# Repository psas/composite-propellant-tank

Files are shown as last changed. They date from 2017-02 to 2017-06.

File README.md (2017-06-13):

# composite-propellant-tank
Prototyping lightweight composite LOX and IPA tanks for LV4.

**The good**: the current PSAS CF airframe technology seems to offer fantastic tank factors if they can be used as propellant tanks, even given extremely conservative mass growth assumptions. This could give us the mass ratios to get LV4 above the von Karman line. Early conceptual design analysis for LV4 suggests that 280x700 mm modules are optimal.

**The bad**: Composites are hard...
- Lack of established design criteria for composite tanks
- Galvanic corrosion of composites in contact with metals
- Composites degrade under extreme temperatures
- Composites degrade in the presence of mositure
- Difficult to detect defective adhesive bonds in composite structures
- Difficult to maintain hermetic seals
- Difficult to incorperate cutouts
- Significant problems with CTE mismatch when used in conjunction with metallic structures

**The Ugly**:  Proof-of-Concept Composite Fuel Tank designed and built by 2017 PSAS Capstone Team. Currently undergoing testing and refinement.

## Summary of 2017 Tank Capstone Project Design Artifacts
* Analysis
	* Calculations (Hand Calculations and Python Scripts)
	* Finite Element Analysis (Code, Results, and Documentation)

* Design 
	* CAD (Current and Archive)
	* Design Ideas

* Documents
	* AIAA (Paper Abstract)
	* Materials (MDS and Property info
	* ME492 (Capstone Docs)
	* ME493 (Capstone Docs)
	* Research Documents (Literature Review Documents)
	* OSGC (Oregon Space Grant Award Info)
	* Presentations (Resources for project presentation)
	* Resource Documents (How Tos and Readme Docs for Git, Jupyter, etc.)
	* Safety (docs related to chemical safety)
	*  Team Documents  (Team Agenda, Meeting notes, Contacts, etc.)
	*  Templates (Experiment Templates)
	*  Doc Readme and Standards of Documentation
	*  Media (Photos and Videos)
	
*  Manufacturing (Procedural documents)
*  Testing (Test results and procedures)

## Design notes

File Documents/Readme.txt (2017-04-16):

Current Working files should be located here.  Once completed/past date, move to appropriate folder or archive.

~NB

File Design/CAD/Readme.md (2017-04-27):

## Model Naming Conventions
Current working models should be located in the Current Folder.  Once adjustments have been made, please move previous
models/designs into the appropriate Archive.

~NB

CAD Model Naming Convention:

Part numbering convention:
####-A (first two digits are type of part, i.e. rings or end cap...etc, last two digits are iteration #)
Liner: 01 series          Example: 0101 is first liner iteration, 0102 is second liner iteration
Rings: 02 series
End cap: 03 series
Al Tape: 04 series
PRV pipe: 05
Gasket: 06
Letters refer to various versions, such as tube liner vs sheet with seam liner
Example: 0201-A is ring designed for sheet liner iteration 1, 0201-B is ring designed for tube liner iteration 2.

A=Sheet liner, B=Tube liner

## Summary of Iterations so far:

- Tank Iteration 1: (Archive/First Tank Assembly) This is a design with a round end cap. 

- Tank Iteration 2: (Archive/Second_model) Has a flat end cap, screw size is 0-80.

- Tank Iteration 3: (current/Flat End Cap Model (.031-in Sheet Liner)) This model uses the thin PTFE sheet that is etched
on one side for bonding. Screws have been updated to size 3-48. The assembly has two options for end caps. There is a flat
end cap and a bell shaped end cap. The flat endcap requires nuts and washers to attach the threaded fittings. The bell shaped
end cap has threading to attach the fittings. Note: to view the bell shaped endcap suppress End Cap<1> and End Cap <2> and unsuppress 
Alternative End Cap and No Holes End Cap. This design requires an aluminum bridge (not shown) to bond the sheet in a tube shape.

- Tank Iteration 4: (current\Flat End Cap Model (0.125-in Tube Liner)) This model uses an 1/8<sup>th</sup> inch tube of PTFE and has a flat endcap

- Tank Iteration 5: (current\Shrink Fit Model (0.125-in Tube Liner)) End cap was modified for a shrink fit design. The sizing for the fitting
portion will be complete when the size calculations are done. We are also considering adding a keyway for hole alignment.

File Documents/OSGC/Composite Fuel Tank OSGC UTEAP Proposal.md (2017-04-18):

**Composite Cryogenic Fuel Tank**

Portland State University

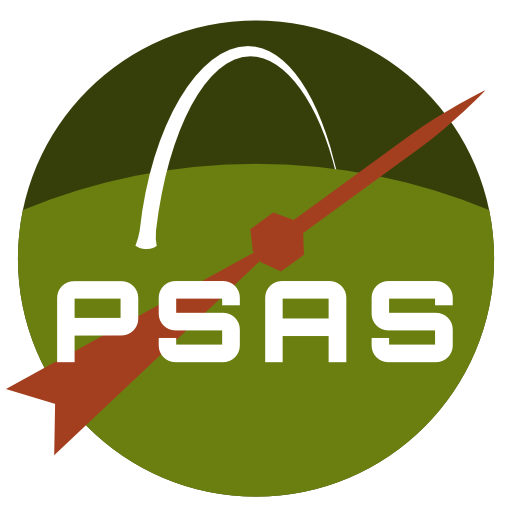
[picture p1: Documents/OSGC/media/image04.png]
{width="1.515625546806649in"
height="1.515625546806649in"}

*Team Lead*

Alex Farias

Undergraduate Student, Department of Mechanical and Materials
Engineering

Portland State University

1323 SE 65th Ave. Hillsboro, OR 97123

(971)770-6017

afarias@pdx.edu

*Project Advisor*

Jun Jiao

Department of Mechanical and Materials Engineering

Portland State University

\(503) 725-4228

jiaoj@pdx.edu

**Date of Submission: 2017-01-16**

**Project Description**

Our research will study the feasibility of a composite, cryogenic fuel
and oxidizing tank for the Portland State Aerospace Society (PSAS) high
altitude amateur rockets (LV3 and LV4). This research will also function
as a senior capstone project to meet undergraduate graduation
requirements in the Portland State University Department of Mechanical
and Materials Engineering.

The rocket will use liquid oxygen (LOX) and ethanol as a propellant.
Therefore, the tank must withstand cryogenic temperatures. Various liner
and insulation materials will be tested to prevent leaking and reduce
thermal stress. We will use FE modeling and destructive testing to
validate our tank design.

In developing a composite tank we need to answer four questions: what is
the geometry of the tank design, what materials are appropriate, how
should the vessel be manufactured, and what are the operating parameters
of the final tank design.

**Tank Geometry**

Our research will focus on developing a multi-layer composite fuel tank
geometry that can accommodate fuel and electrical feed lines within the
pre-existing LV3 airframe module design or, alternatively, substituting
an entire airframe module with an independent fuel module. However, the
primary goal of our project is not necessarily a fully flyable fuel
tank, but initial feasibility testing and analysis.

**Manufacturing Processes**

We will use hand layup techniques pioneered by the PSAS carbon fiber
airframe design (LV3) to manufacture composite layers for the cryotank.
We will create a laminate skirt similar to the one used in the NASA
Composite Cryotank Technologies and Demonstration (CCTD) Project[^1] to
allow the tank to mate with adjacent components and provide structural
support for external loading.

To apply composite material in the desired tank geometry, aluminum rings
are attached to a cylindrical mold with spherical ends. Plain weave
carbon fiber, structural adhesive, and Nomex honeycomb are placed on the
aluminum rings using a hand layup technique. The composite is compressed
onto the mold with a vacuum bag and the module is placed in an oven to
cure the epoxy. This layering technique and corresponding ring design
are expected to be modified according to addition of materials, changes
in layering methods, and tank geometry requirements.

**Material Selection**

Materials are selected based on their compatibility with LOX which has a
boiling temperature of -182.9ºC at 1 atm and is a powerful oxidizer.
Current layering materials under consideration include carbon fiber
composite (structural material), PTFE (chemical insulator), and Cryogel
(thermal insulator). To prevent liquid oxygen from leaking into the
composite layers, a Teflon (PTFE) liner is desirable due to its
excellent mechanical and thermal properties at cryogenic temperatures.
The optimal composite liner will be determined by comparing a spray on
coating of PTFE resin wetting agent with a liner made of PTFE resin
granular molding powders that is compression molded to the tank geometry
and sintered. An insulation layer such as spray on foam, aerogel, and
cryogel are considered to create a thermal barrier between the LOX and
the composite layers. These materials are preliminary test materials and
subject to change based on the results of further research and testing.

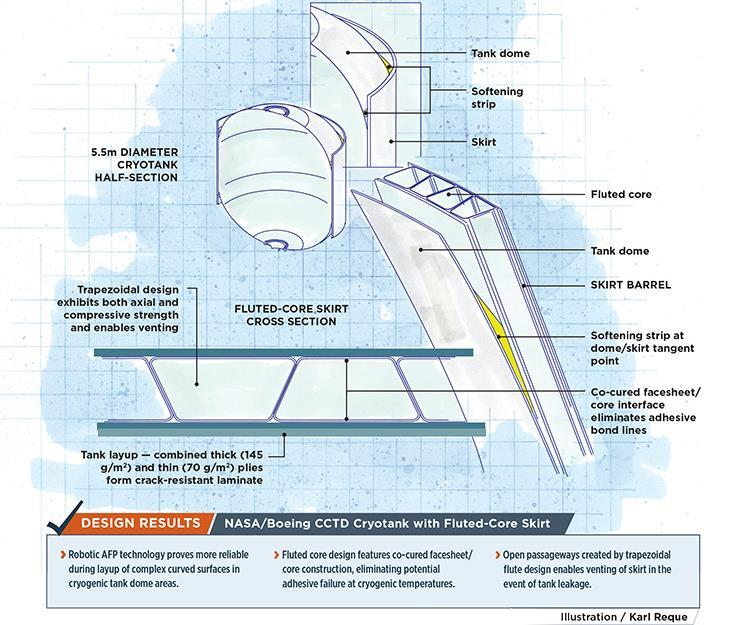
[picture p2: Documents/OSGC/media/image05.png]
{width="4.296875546806649in"
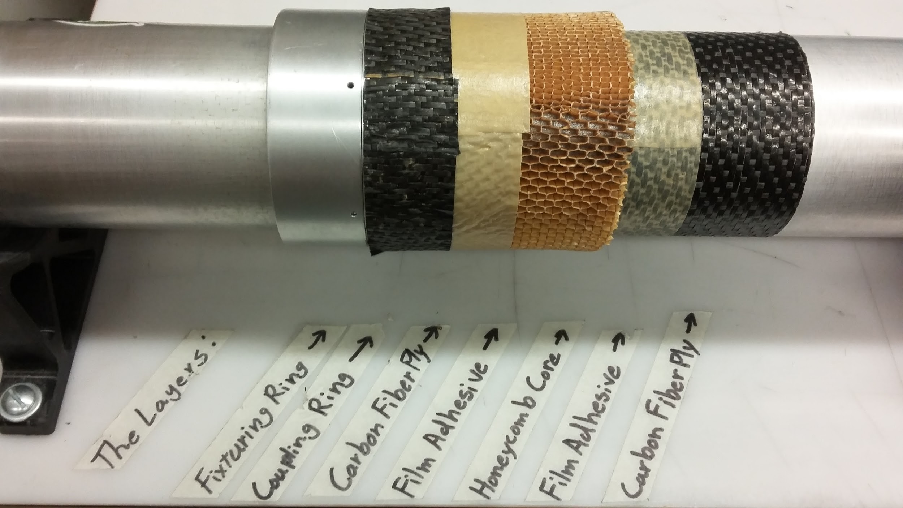
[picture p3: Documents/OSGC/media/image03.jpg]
height="3.5677088801399823in"}{width="3.682292213473316in"
height="2.0494706911636045in"}

  *Figure 1: NASA/Boeing CCTD Cryotank with Fluted-Core Skirt. Illustration: Karl Reque*   *Figure 2: 2015-2016 Composite PSAS airframe layer configuration*
  ---------------------------------------------------------------------------------------- -------------------------------------------------------------------

**Testing**

We will conduct hydrostatic testing on the prototype to determine the
maximum allowable working pressure (MAWP) of the tank. According to
ASME, section VIII, Pressure Tests, MAWP = Minimum Hydrostatic Test
Pressure/(1.3\*LSR), where LSR is the lowest stress ratio of the
allowable stress at test temperature to the allowable stress at design
temperatures. Microfracture and material degradation analysis will be
performed on cryogenically-treated sample composite coupons using
microscopy equipment available in the Center for Electron Microscopy and
Nanofabrication.

We will perform a thermal fluid analysis of the fill and drain operation
to gain an understanding of the thermal stress the tank will encounter
at the composite-aluminum and composite-layer interfaces. The cryogenic
test will consist of filling the tank with liquid nitrogen, waiting for
steady-state conditions, and draining the tank. Sensors will be used to
measure the temperature, pressure, strain, and heat flux during testing.

*Table 1: **Key Milestones and Deliverables** (01/09/17 - 06/12/17)*

  ---------------------------------------------------------------------------------------------------------------------
  Week 1-3     Select insulation material and polymers based upon cost and material properties.
               
               Devise and test polymer deposition techniques with refined selection of materials.
  ------------ --------------------------------------------------------------------------------------------------------
  Week 4-6     Create SolidWorks design for aluminum rings and easy access fill-ports.
               
               Perform thermal and mechanical stress/strain analysis with FEA simulations.

  Week 7-9     Interface tank components and complete composite layup for tank prototype.

  Week 10-12   Perform hydrostatic tests to determine working tank pressure.

  Week 13-15   Perform cryogenic tests to assess aluminum ring/composite interface.
               
               Test fill with LOX, pressurize, and test fire using PSAS 3D printed engine and liquid fuel test stand.

  Week 16-18   Organize and complete documentation for final report and presentation
  ---------------------------------------------------------------------------------------------------------------------

**Scholarly Aspects and Educational Objectives**

The composite cryogenic fuel tank project will give our team an
opportunity to learn how to design parts for manufacturing, fabricate
composite materials, test prototypes, and create technical documents to
report procedures and results. This experience will directly support the
main objective of the PSU capstone which provides students with
teamwork, project management, communication, and engineering experience
to prepare us for our careers following graduation. This project also
provides invaluable experience attacking an open-ended problem in which
the team must make design decisions without a clear list of constraints,
since all design parameters are codependent within the greater PSAS LV4
Rocket Project.

**Expected Outcomes**

Amateur and University rocket teams are making huge strides to create
rockets that can reach the Von Karman line (100 km), but most teams are
limited by using heavy aluminum tanks. Switching from aluminum to carbon
fiber material has the potential to increase rocket performance by
reducing a dramatic amount of weight. If we are successful, LV4 can
carry larger payloads and give the academic community an opportunity to
do research in suborbital space. Since PSAS is open source, our research
will also provide further insight on composite cryogenic propellent
tanks and will pave a path for future composite tank designs.

**Synergy**

**Team-Advisor Collaborative Learning**

The composite cryogenic fuel tank project is essentially a recursive
design problem-- What combination of geometry and material produces a
structurally and chemically sound LOX fuel tank? This question presents
a number of research, design, and testing challenges that require both
mechanical and material engineering solutions. This team’s experiential
background is primarily mechanical; our project advisor, Dr. Jun Jiao,
is an experienced materials engineer. This combination encourages our
team to take full advantage of the team-advisor relationship to learn
about proper manufacturing and testing processes (and how to make
informed selections of structural and insulative materials) as we test
various geometries and layering techniques.

Additionally, Dr. Jiao’s position, as Director of the Center for
Electron Microscopy and Nanofabrication, makes various material testing
equipment and resources (including a cryogenic probe station) available
to our team-- resources that would not otherwise be easily accessible to
an undergraduate research team. Dr. Jiao has also served as a conduit to
industry donors for past PSAS capstone teams, helping them get access to
proprietary materials such as the Boeing carbon fiber sheets that serve
as the basis for the current PSAS composite airframe. As the PSAS
rockets’ design requirements increasingly require the development of
custom build materials, we hope to develop and reinforce the
relationship between PSAS and the Material Science department through
our collaboration with Dr. Jiao on this project.

**Leveraging Opportunities for Funding or Further Research**

Regardless of the outcome, the results of this project’s research will
have implications for other PSAS projects. Knowing whether or not a
composite cryogenic fuel tank is feasible given the resources we have
access to, and knowing its limitations, will inform how all future
rocket airframes are designed and built. For example, if a composite LOX
fuel tank is viable, but only at relatively low pressures, then that
provides constraint parameters for the PSAS Electric Feed System
capstone team, which is attempting to substitute the current, heavier
pressure-fed system that relies on highly pressurized fuel tanks. If we
determine that a composite tank could function at higher pressures, or
the electronic feed system cannot work within the constraints provided
by the fuel tank design, then the incentive becomes to refine the
pre-existing feed system.

If PSAS can reduce the dry weight of the rocket by integrating a
composite cryogenic fuel tank and/or an electronic propellant feed
system, then building a small-scale rocket that will reach the Von
Karman line becomes feasible and launching a nano-satellite (PSAS’
ongoing CubeSat project) into low-earth-orbit becomes a viable target
goal for a university aeronautics team. This is a novel realm for
university-level rocketry : to our knowledge, no university club has
successfully flown a rocket beyond the Von Karman line. Such a flight
would likely generate public and academic interest that could be
leveraged for further funding and support from a range of institutions,
organizations, and private donors.

This project also fulfills the requirements of a senior mechanical
engineering design capstone project for the 6 primary members of the
team and will provide the opportunity to develop general engineering and
aerospace-specific skills in the subject areas of design, structural and
thermal analysis, material science, and manufacturing.

The goal of this project is not just to advance the knowledge and
resources of PSAS and its teams, but to methodically document and share
this project’s findings and make them available to the public. This
serves to educate and encourage other academic groups to advance their
rocketry research and development. Contributing to the growth and wealth
of research in this field is always an underlying goal.

**Aerospace Relevancy**

The NASA Space Technology Mission Directorate’s Game Changing
Development (GCD) Program supports the CCTD project, where NASA and
Boeing engineers aim to improve composite cryogenic tank technology for
heavy lift vehicles and other in-space applications. Success in the CCTD
project could lead to rocket fuel tanks that are more than 30 percent
lighter and offer lower cost for payload delivery to orbit[^2].

If the composite cryogenic fuel tank research is successful, our tank
design has the potential to make the LV3/LV4 rocket fuel tanks
significantly lighter than their aluminum counterparts, which would
allow PSAS to carry larger payloads, such as a cubesat, to lower Earth
orbit.

Similar to NASA’s Human Exploration and Operations Launch Services
Program, PSAS could provide lower earth orbit research opportunities to
the academic community. Further development in composite cryotank
technology will lead to more cost effective space travel, not only for
professional ventures involving larger firms such as NASA, but
additionally for university or amatuer venture launches.

**Budget**

This budget includes materials and services necessary to prototype our
composite fuel tanks. It also includes previous and future in-kind and
services donations.

  **Item**                           **Description**                                                      **Vendor**                 **Amount**    **Matching**
  ---------------------------------- -------------------------------------------------------------------- -------------------------- ------------- --------------
  6061 Aluminum                      Material for rings and mold                                          Metal Supermarket          \$800         
  Machinable Foam                    Material for composite mold                                          Sailrite                   \$200         
  Liquid Nitrogen                    40 gallons of liquid nitrogen for fill and drain cryogenic testing   PSU Chemistry Stockroom    \$140         
  Liquid Nitrogen Handling           Protection equipment                                                 PSU Chemistry Stockroom    \$100         
  Liquid Oxygen                      40 gallons of liquid oxygen for cryogenic test                       Airgas                     \$200         
  Aluminum Foil                      1000 sq ft. insulation material                                      Uline                      \$43          
  Cryogel Z                          30 sq ft. insulation material                                        Aspen                      \$900         
  PTFE                               Molding powder, and resin wetting agent for tank liner               Chemours                   \$1,800       
  Plain Weave Carbon Fiber Prepreg   Composite material                                                   Pacific Coast Composites                 \$3,500
  Nomex Honeycomb                    Core material for composite                                          Pacific Coast Composites                 \$2,000
  Meltbond                           3M composite structural adhesive                                     Pacific Coast Composites                 \$2,500
  Aluminum mating rings              Material and machining for manufacturing mating rings (12 rings)     Machine Sciences                         \$3,600
  Layup Mandrel                      Mold for composite layup                                             Arrow                                    \$350
  Aluminum dummy layup rings         Mold assembly part                                                   PSU Melt                                 \$180
  Mechanical Components              Seals, gaskets, plumbing fittings                                    Various Vendors            \$1,000       
  Sensors and Gauges                 Sensors and gauges for cryogenic testing                             HBM                        \$1,500       
  Discretionary Machining Labor                                                                                                      \$2,000       
  Sandpaper                          Sandpaper of varying grit                                            Home depot                               \$50
  Vacuum Bagging Material            Vacuum bags, Breather fabric, sealant tape, and release film         Fiberlay                                 \$770
  Vacuum Pump Equipment              Pump regulator, pump oil, reducer adapter, hose                                                               \$180
  Orca Seal                          Solvent for mold surface treatment                                   Fiberlay                                 \$130
  Orca Clean                         Solvent for mold surface treatment                                   Fiberlay                                 \$100
  Compression molding material       Shrink tape, kapton tape, industrial scissors, ceramical             Various Vendors                          \$230
  Heat gun                           Heat gun for composite layup                                         Milwaukee                  \$180         
  Dr. Jun Jiao's Time                1 hour per week, Jan - Jun (20 weeks) at \$100/hr                                                             \$2,000
  Future Material Donations          Future material donations from Boeing, Pacific Coast Composites                                               \$6,000
  Future Services Donations          Material and machining time from Machine Sciences Corporation                                                 \$3,000
  **Total**                                                                                                                          **\$8,863**   **\$24,590**

**Team Lead Resume**

**Alex K. Farias**

1323 SE 65^th^ Avenue, Hillsboro, OR 97123

\(971) 770.6017 \~ afarias@pdx.edu

**EDUCATION**

**Bachelor of Science in Mechanical Engineering** (09/14/2015 –
06/21/2017)

*Portland State University, Portland, OR*

**COURSE HIGHLIGHTS**

Heat Transfer, SolidWorks, Fluid Mechanics, Thermodynamics, Experimental
Design, Finite Element Analysis, Material Science, Technical Writing,
Engineering Economic Analysis

**CERTIFICATION**

· SolidWorks Associate, Certificate ID: C-UVWU2UYBK5

**SOFTWARE AND COMPUTER SKILLS**

· Working knowledge of finite element method using Abaqus

· Proficient with MS Word, Excel, and PowerPoint

· Proficient with MATLAB and R data analysis software

· Familiar with C++ programming language

**EXPERIENCE**

**Student Member** (01/2016 –Present)

*Portland State Aerospace Society, Portland, OR*

· Designed rocket part assemblies and technical drawings using
SolidWorks

· Machined aluminum rocket parts using mill and lathes

· Fabricated composite rocket airframe using hand layup and compression
molding techniques

**PSU Student Chapter Team Member**, (01/2016 –07/2016)

*Engineers without Borders, Portland, OR *

· Analyzed design options for sustainable hand washing station at
developing Ethiopian school

· Prepared alternative analysis report to validate hand washing station
design

**Office Assistant** (03/2015 – Present)

*Portland Community College Jobs & Internships Department, Portland, OR*

· Performed research to assist with project development

· Evaluated course curriculum and provided recommendations to fix issues

· Coordinated logistics with business partners participating in campus
events

· Evaluated department statistics to optimize resources

· Organized department records and processed confidential documents

· Created presentations used for student development

**Assistant Manager** (06/2012 - 12/2015)

*Portland Community College Bookstore, Portland, OR*

· Responsible for overseeing day-to-day store operations

· Managed group projects and reported progress to supervisors

· Provided training, support, and guidance in team oriented environment

· Coordinated shipping and receiving to ensure on-time delivery for high
volume orders

**Portland Community College STEM Club Volunteer** (09/2014 & 09/2015)

*OMSI Maker Faire, Portland, OR*

· Trained volunteer members to use CNC machines and software

· Demonstrated CNC and Laser Cutting technology to community members

**Team Member Listing and Experience Profiles**

*Group Demographics:*

Male/Female Students: 5/1

Underrepresented minorities: 2 Hispanic students

*Neil Benkelman*: (Mechanical Engineering Undergraduate, PSU)

Past project experience developing autonomous navigation and hazard
avoidance platform for use with a drone, fluid dynamics, heat transfer,
FEA, data analysis software (R and MATLAB), machine shop access.

*Russell Berger* (Mechanical Engineering Undergraduate, PSU)

Experience with manufacturing composite airframe parts for Atomic
Aviation, advanced fluid mechanics, phase transformation and kinetics of
materials, SolidWorks, and owns a 3D printer. Experience with data
analysis software (R & Matlab), as well as CAM software for CNC
machining, and machining with emphasis on lathe.

*Alex Farias* (Mechanical Engineering Undergraduate, PSU)

Experience with SolidWorks, manufacturing composite airframe for PSAS
rocket, FEA, advanced fluid mechanics, data analysis software (R and
Matlab), and machining with lathes and mills.

*Francesca Frattaroli*: (Mechanical Engineering Masters Pathway
Undergraduate, PSU)

Biogeochemistry lab and field technician. Experience in designing and
prototyping low‐cost sensor apparati for environmental research, data
analysis software (R and Matlab), FEA, Advanced Fluid Mechanics and
machine shop experience (mills and saws).

*Weldon Peterson*: (Mechanical Engineering Undergraduate, PSU)

Experience with lathe and milling processes, Solidworks, machining
design, geometric dimensioning and tolerancing, data analysis software
(R and Matlab). Also previously experience with liquid oxygen as a fuel
in glass studio and great group dynamic with the rest of the team.

*Christopher Wilson*: (Mechanical Engineering Undergraduate, PSU)

PSAS member, Experience with geometric dimensioning and tolerancing,
controls, laser cutters and 3d printers, machine shop access with minor
experience on the mill and lathe, data analysis software (R and Matlab).

[^1]: [*https://ntrs.nasa.gov/archive/nasa/casi.ntrs.nasa.gov/20130013009.pdf*](https://ntrs.nasa.gov/archive/nasa/casi.ntrs.nasa.gov/20130013009.pdf)

    Structures and Design Phase I Summary For the NASA Composite
    Cryotank Technology Demonstration Project. 2013

[^2]: [*https://gameon.nasa.gov/projects-2/archived-projects-2/composite-cryogenic-propellant-tank/*](https://gameon.nasa.gov/projects-2/archived-projects-2/composite-cryogenic-propellant-tank/)

    Composite Cryotank Technologies and Demonstration (CCTD)

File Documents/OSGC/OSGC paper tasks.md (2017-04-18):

Task Delegation:

Project Description: Alex

Synergy: Francesca

Aerospace Relevancy: Chris

Faculty letter of support: ??

Bill of materials:

What do we need?

-PTFE powder

-Aluminum for mold

-Cryogel

-Mylar

-Do we have access to a Hydraulic Press?

-Cost of labor to manufacture parts? (ask andrew for ballpark)

We need to call places and ask for quotes

Model composite tank with a blow down system

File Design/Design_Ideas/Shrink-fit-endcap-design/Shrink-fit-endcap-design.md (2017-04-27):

# Ideas surrounding a shrink-fit endcap design:

## Main arguments for:

PTFE has a larger coefficient of thermal expansion than aluminum at all temperatures. By adding an extended lip to the endcap that the PTFE can clamp down on during the cryo-fill process, a mechanical seal can be formed, isolating the LOX from the CF and adhesive. The End-cap can be shrunk with LN2 prior to insertion, allowing for a compression of the PFTE prior to fill, so a seal can be established at room temp. This solution also reduces complications related to layer separation and simplifies the layup procedure by eliminating the need to etch and adhere the PFTE to the CF structural layers (LOX sealant can be put in at this interface).

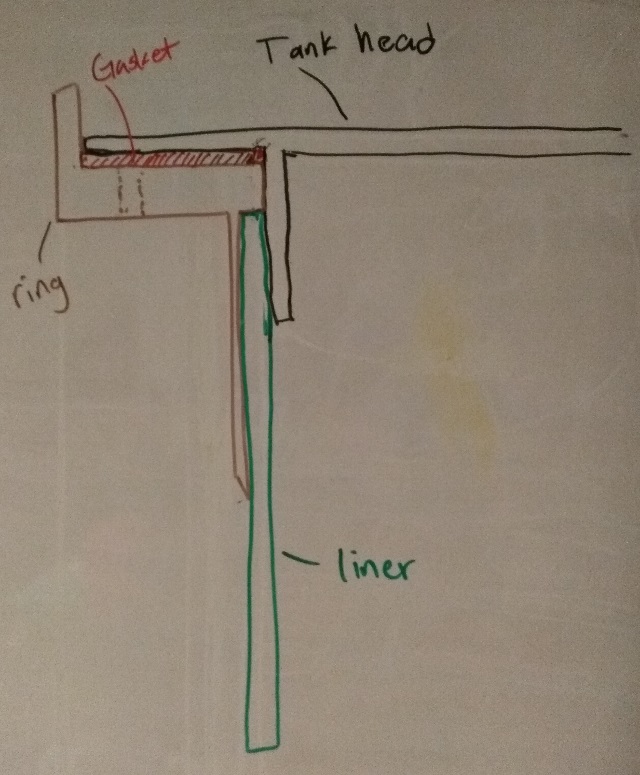
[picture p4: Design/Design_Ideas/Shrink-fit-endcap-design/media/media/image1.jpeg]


### Potential concerns:

-Excessive PTFE contraction leading to cracking of PTFE or permanent deformation of PTFE that prevents reuse of the tank.

## Analysis to do:

Q: How to compress the PTFE and properly retain the lox seal during the chill process?

* Calculate the unrestricted expansion expected in the radial direction of the inset endcaps when subjected to shrink fit - expansion (use to define PTFE overhang)

* Calculate final diameters of PTFE and AL when both subjected to cryo-temps

* Devise initial test procedures.

## Build to do:

* simplified ring and endcap designs without complex geometry and screw holes.

* cut shorter virgin PTFE tubing for testing.

## PTFE Properties: 

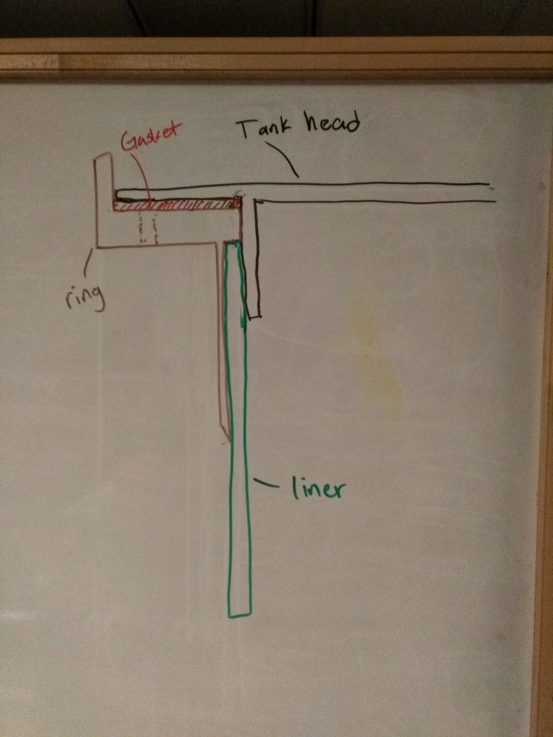
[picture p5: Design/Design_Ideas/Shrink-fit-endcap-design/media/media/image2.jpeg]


-Fairly uniform compressive strength across PTFE grades

-Inert when exposed to LOX (unless there is contamination, pigmentaiton, or filler present)

-Deformation under load: max 50% (at 1000 psi over 24 hrs)

-Thermal conductivity: 0.2+/- 0.04 W/m\*K

-Yield strength of teflon at -196C = 131 MPA, 19,000 PSI

-Meaning the PTFE should bounce back to its original dimensions when cooled, assuming

-it is only elastically compressed.

-Mod E of Teflon PTFE = 56.9-326 ksi (Quite a range)

-CTE of Teflon PTFE (+25 to -190C) = 86e-6 +/- 3e-6 (1956 Kirby text)

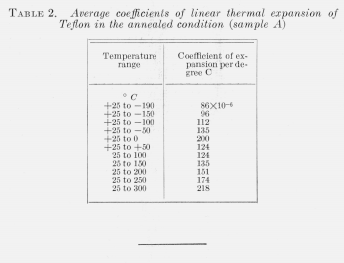
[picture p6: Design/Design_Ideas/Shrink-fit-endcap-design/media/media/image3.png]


### Aluminum Properties

Mod E of AL6061 = 10000 ksi

CTE of AL6061 = starting at 23e6 and decreasing with temperature

Yield Strength of AL6061 at -190C: 47, 000Psi

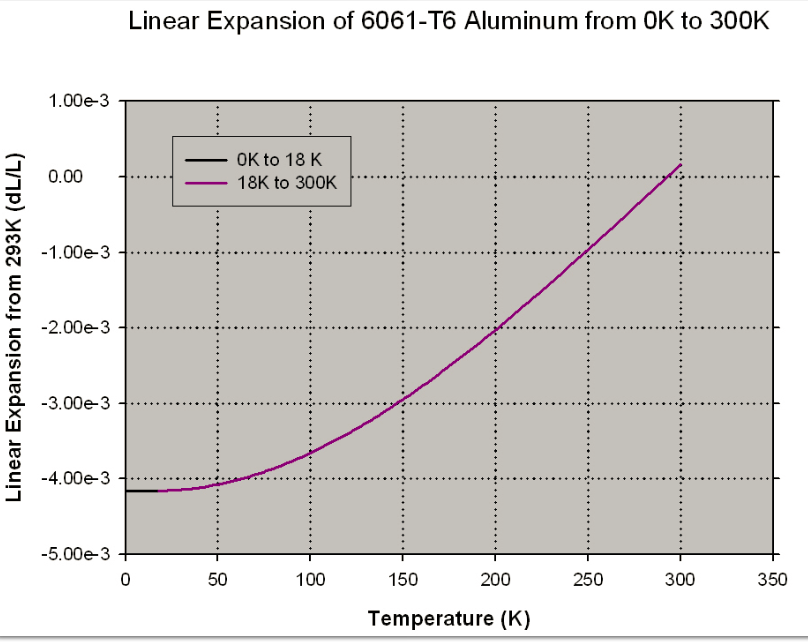
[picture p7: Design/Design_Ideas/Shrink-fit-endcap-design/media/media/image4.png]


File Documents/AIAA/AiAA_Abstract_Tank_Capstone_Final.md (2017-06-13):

**Design and Manufacture of Composite Liquid Oxygen Propellent Tank for
University Rocket**

Neil Benkelman, Russell Berger, Weldon Peterson, Alex Farias, Francesca
Frattaroli, and Christopher Wilson

*When designing a rocket to overcome Earth’s gravitational force, the
dry mass of the propellent tank is the most limiting factor for amateur
and university-level rocket teams. Most rocket groups are dependent upon
heavy aluminum tanks to hold their liquid propellant. Single-piece,
carbon-fiber composite tanks are strong and light, but require expensive
automated fiber placement techniques that are not a viable option for
amateur teams, who operate with a tight budget and limited resources in
comparison to their corporate or government counterparts. Portland State
University’s composite-tank capstone and research project is an attempt
by senior undergraduate engineering students to design, build, and test
an affordable, lightweight, composite liquid oxygen (LOX) propellant
tank for eventual integration into Portland State Aerospace Society’s
100 kilometer rocket.*

I.  **Introduction**

For the past decade, amateur and university rocketry groups have been
undertaking an impromptu space race to breach the Von Karman Line (100
km above earth’s surface). The greatest barrier to success is the ratio
of the mass of the fueled rocket to its dry mass. This is commonly
referred to as the mass ratio. Tsiolkovsky’s rocket equation shows that
the mass ratio must increase exponentially with the rocket’s change in
velocity. In simpler terms, if you want to go faster and higher you must
decrease your dry weight, and small weight savings make a large
difference. Conventional amateur and university rockets are constrained
to lower altitudes by the use of either solid propellant or liquid
propellant housed in aluminum fuel tanks with relatively low mass
ratios. A mechanical engineering senior capstone group at Portland State
University is working to mitigate this dry mass limitation by designing
a liquid oxygen propellant tank out of primarily composite materials
which will be much lighter than all-aluminum equivalents. This design
requires the development of corresponding manufacturing techniques that
take into account the differing thermal, chemical, adhesive and
structural properties of the composite materials, and their need to
interface with each other, and with aluminum components.

Two previous PSAS capstone groups have focused on improving the overall
dry-weight of the PSAS LV3 rocket, a third generation solid-propellant
rocket. The 2014 and 2016 Airframe capstone teams developed a unique
carbon-fiber composite layup technique[^1], in which layers of carbon
fiber, adhesive, and nomex honeycomb were laid up onto 6-inch aluminum
mating rings, producing 18-inch airframe modules that were then mated
together to form the body of the LV3 rocket. Having significantly
reduced the mass of the rocket in this way, PSAS is seeking to reduce
the mass of the internal components, starting with the propellant tank
module.

II. **Significance**

Being able to design a working, lightweight, liquid-propellant tank
using resources accessible to a university student organization, will
not only assist the PSAS community in achieving its goal of breaching
100km and exploring high altitude science by putting a cubesat into
orbit, but provide the greater rocket community with a more affordable
and accessible tank design. Due to its nature as an open source project,
all results will be posted publicly, allowing any future university or
amateur team to benefit. Additionally, the financial and technical
constraints of this project also pose an opportunity to develop unique
solutions to the problem of cryotank design that could benefit industry
and science as a whole.

III. **Plan of Work**

The scope of this project builds on the previous work of other student
groups. As previously noted, a 2016 capstone group developed a layup
process and design of a lightweight composite airframe. Investigation
into what techniques, procedures, and materials that can be adapted from
this project are already underway. Additionally, research into composite
cryotank technology,[^2] and associated methods and safety protocols has
already been done before; PSAS has aggregated hundreds of relevant
technical papers and NASA procedural documents which are currently being
evaluated by the design team and are expected to inform initial designs,
material selection, and testing methods.

Substantial material resources were donated by Boeing and other industry
sponsors (8-139 prepreg, 8-222 Cycom 6070/7781, BMS 8-308C 60001, etc.)
to PSAS for use with the 2016 capstone and have since been acquired to
be used with this Composite Tank design. Existing material resources and
composite layering techniques will be tested first, for structural
integrity at cryogenic temperatures, before other materials are
considered for testing. At the initial design stages, there are many
options under consideration: composite types, layering methods, tank
geometries, assemblies, and manufacturing procedures will all be
researched, developed, and tested for viability at cryogenic
temperatures and launch loading conditions.

{width="4.296875546806649in"
height="3.5677088801399823in"}{width="3.682292213473316in"
height="2.0494706911636045in"}

  *Figure 1: NASA/Boeing CCTD Cryotank with Fluted-Core Skirt. Illustration: Karl Reque*   *Figure 2: 2015-2016 Composite PSAS airframe layer configuration*
  ---------------------------------------------------------------------------------------- -------------------------------------------------------------------

The project is currently in a research and project design phase, along
with preliminary material testing and assembly design. During this
phase, major design constraints, challenges, and corresponding testing
methods are being identified, along with best practices of
documentation, analysis, and evaluation. Major challenges already
identified include-- designing tank mating rings to interface with air
frame, matching the form factor of an airframe module, developing
aluminum tank endcaps to interface and seal with composite body,
providing adequate chemical and thermal insulation, and developing a
layup of selected materials to fit onto final geometry.

In identifying viable designs, an iterative design process, coupled with
material testing (thermal, tensile, and impact) and finite element
analysis (body force and thermal stress analysis) will first be
conducted. This will be followed by the fabrication of multiple scale
prototypes of designs or design combinations that proved successful.
Prototypes will then be subjected to both hydro and cryo testing
procedures to identify leaks, rates of thermal conduction, oxygen
diffusion, and microcracking and points of structural failure. Given
time, there is potential for a full-scale (LV3-size) prototype tank,
subject to the same testing methods and analysis. Capstone requirements
dictate that this research project and associated documentation be
completed by mid-June 2017.

The ultimate goal is to produce a subscale cryogenic fuel tank that can
safely contain liquid oxygen at operational pressures (3 ATM[^3]) and
temperatures (-183 ℃) for the duration of the rocket pre-launch
procedure (approx. 1 hour, depending on tank scale). Documentation of
measurements, test methods, and development procedures are of equal
importance to successful project completion. This emphasis on
documentation is in line with PSAS’ educational mission to advance
amature and university-level rocketry by making all of its research and
discoveries available to the public.

**Appendix**

i\. System requirements-measurements matrix.

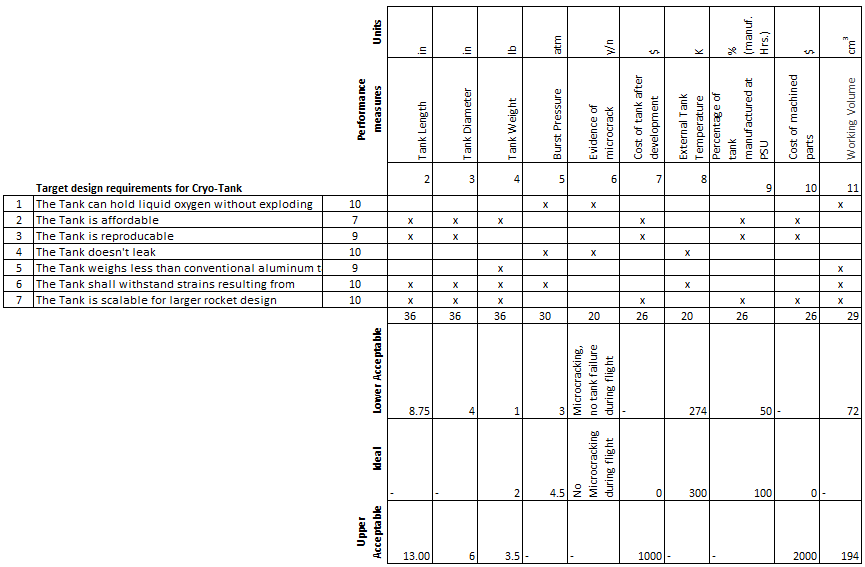
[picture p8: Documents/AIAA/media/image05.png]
{width="8.401042213473316in"
height="5.468009623797025in"}

[^1]: Shields, J. P., and Elwood, L., “Design and Manufacture of an
    Open-Hardware University Rocket Airframe using Carbon Fiber,” *AIAA
    SPACE 2016*, American Institute of Aeronautics and Astronautics,
    2016.

[^2]: Johnson, T. F., Sleight, D. W., and Martin, R. A., “Structures and
    Design Phase I Summary for the NASA Composite Cryotank Technology
    Demonstration Project,” 2013, pp. 1–11.

[^3]: Three ATM is a relatively low pressure for a propellant tank of
    any size. This low pressure is made possible by the parallel PSAS
    development of an electric feed system that will replace the current
    blowdown system for the LV4 rocket.

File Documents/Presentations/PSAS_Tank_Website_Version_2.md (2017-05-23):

---
layout: project
title: PSAS Composite Fuel Tank 
sponsor: Portland State Aerospace Society
sponsor_url: http://www.psas.pdx.edu/
document-date: 15 May 2017
---

## Project Objective

The objective of this project is to develop a design and a manufacturing process for a composite fuel tank intended to hold liquid oxygen propellant for use in the Portland State Aerospace Society's LV4 rocket. 

## Team

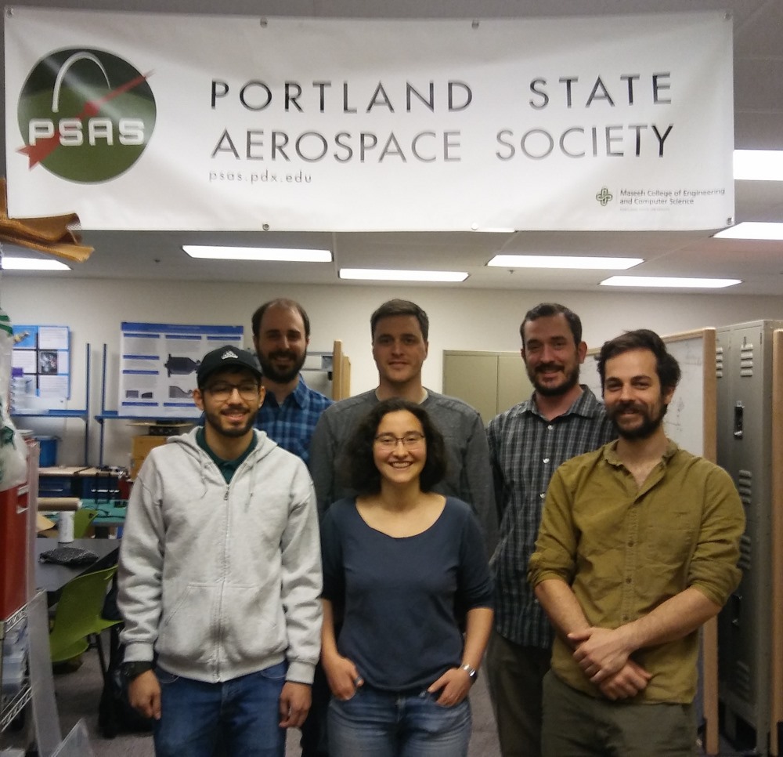
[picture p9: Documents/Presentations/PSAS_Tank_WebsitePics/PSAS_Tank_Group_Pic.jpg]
Team Rocket


The project team is

* Neil Benkelman
* Russell Berger
* Alex Farias
* Francesca Frattaroli
* Weldon Peterson
* Chris Wilson

## Customer/Market Requirements

PSAS requires a composite fuel tank that ...

- is liquid oxygen (LOX) safe for duration of fill cycle and launch (30 minutes to 1 hour).
- does not fail (leak, fracture, or explode) when pressurized to 6 ATM (x2 operational pressure)
- Won’t fail at expected scaled LV4 flight loadings (meets Factor of Safety = 2) for combined loads of thermal and propellant stresses.
- has a manufacturing process which can be performed in the ME department machine shop, or outsourced for a reasonable fee (<$500 per component, assuming max of 1-3 outsourced components).

## Design Challenges

The team's primary design challenges are isolating the LOX fuel from reactive materials, such as the structural Carbon Fiber layers, and maintaining a seal at room-temperature, as well as at cryogenic operational temperatures. An additional challenge is confirming the structural integrety of the pre-existing carbon-fiber airframe at cryogenic temperatures and operational pressures.

## Outcomes

The team has developed two tank designs that take the current PSAS airframe design and incorporate a LOX-compatable PTFE liner to chemically insulate the tank from LOX. The first design employs aluminum mating rings lined with a PTFE tube and sealed with shrink-fit aluminum end-caps to mechanically seal the LOX off from the atmosphere as well as the rest of the airframe structure at room and cryogenic temperatures. The advantage of this design, if successful, is that the LOX will only be in contact with PTFE and Aluminum, materials tested and used in LOX environments with success.
The second design utilizes a PTFE sheet liner held together with an aluminum bridge - generating a potential adhesive-lox interface to be mediated with LOX sealant. The endcaps of the sheet liner design are sealed to the aluminum mating rings with bolts and a PTFE gasket. The advantage of this design, if successful, is the affordability and ease of production, as it would require only an additional layer be added to the current airframe layup process.

### *ShrinkFit Tank Design*

{:.center}
ShrinkFit Tank representation
<figcaption class="center">
Figure 1: ShrinkFit Tank CAD
</figcaption>

The following image shows an exploded view of our shrinkfit tank design.

{:.center}
layer representation
<figcaption class="center">
Figure 2: ShrinkFit PTFE Tube Tank Exploded View CAD
</figcaption>

### *Sheet Liner Tank Construction*

{:.center}
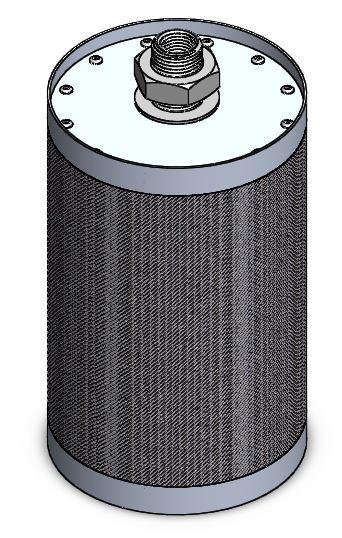
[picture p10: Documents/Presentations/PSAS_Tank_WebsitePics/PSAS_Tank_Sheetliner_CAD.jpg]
Sheet Liner Tank representation

<figcaption class="center">
Figure 3: Sheet Liner Tank CAD
</figcaption>

The following images show the current layup process, using the sheet liner tank design layup and a completed tank.

{:.center}
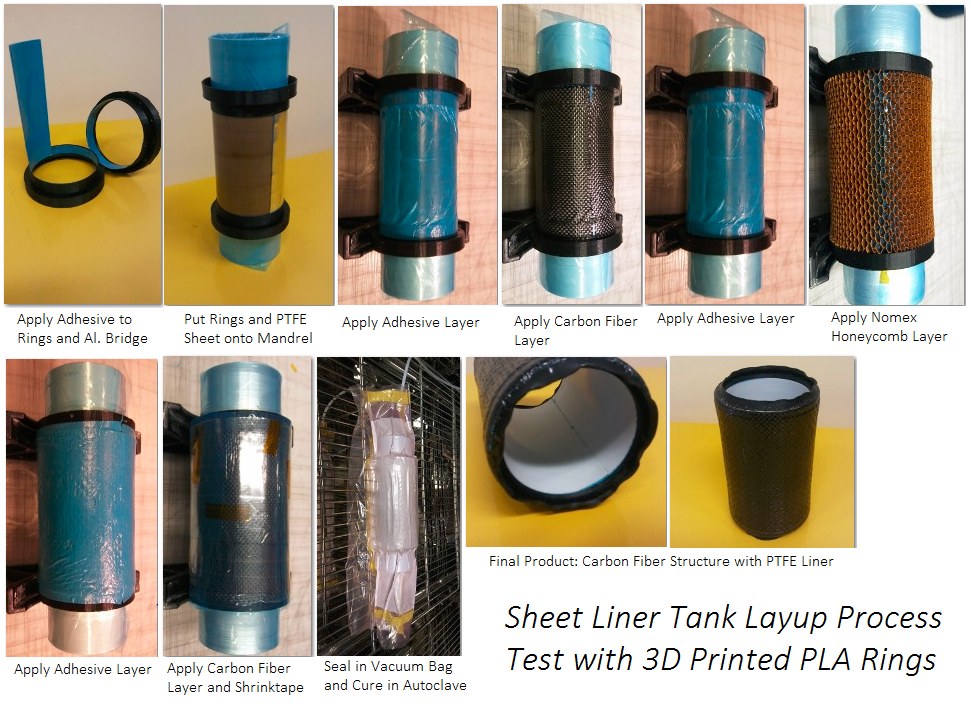
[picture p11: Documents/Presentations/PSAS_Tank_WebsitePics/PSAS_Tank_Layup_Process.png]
Sheet Liner Tank Layup

<figcaption class="center">
Figure 4: Sheet Liner Tank Layup on Prototype PLA Rings
</figcaption>

{:.center}
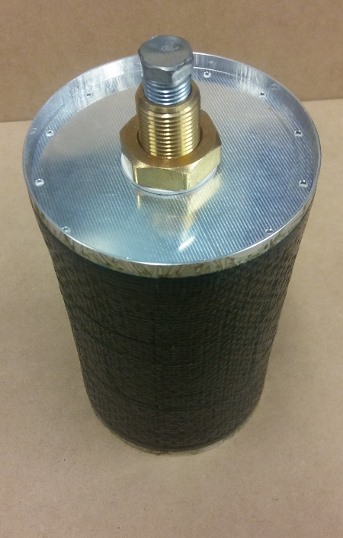
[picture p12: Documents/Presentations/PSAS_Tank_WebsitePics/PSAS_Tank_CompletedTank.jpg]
Shrinkfit Completed Tank

<figcaption class="center">
Figure 5: Sheet Liner Completed Tank
</figcaption>

Material cryotesting has been performed to ascertain the material properties of the PTFE, in order to create a more accurate FEA model of the tank and allow for optimization of design geometry. Complete prototypes of the two tank designs are currently being built and are being compression and hydro-burst tested at cryotemperatures to determine strength and modes of failure. Tests assessing the reactivity and transport of LOX at the various tank interfaces and pressures is to begin shortly. The tank shown to most successfully withstand structural stresses without leaks or fracture and LOX exposure without chemical reaction will be selected as the tank design recommended to PSAS.

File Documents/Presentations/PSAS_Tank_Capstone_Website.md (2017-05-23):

---
layout: project
title: PSAS Composite Fuel Tank 
sponsor: Portland State Aerospace Society
sponsor_url: http://www.psas.pdx.edu/
document-date: 25 April 2017
---

## Project Objective

The objective of this project is to develop a design and a manufacturing process for a composite fuel tank intended to hold liquid oxygen propellant for use in the Portland State Aerospace Society's LV4 rocket. 

## Team

Team Rocket

The project team is

* Neil Benkelman
* Russell Berger
* Alex Farias
* Francesca Frattaroli
* Weldon Peterson
* Chris Wilson

## Customer/Market Requirements

PSAS requires a composite fuel tank that ...

- is liquid oxygen (LOX) safe for duration of fill cycle and launch.
- does not fail when pressurized to 6 ATM.
- won’t fail at expected scaled LV4 flight loadings (meets Factor of Safety =2) for combined loads of thermal and propellant stresses.
- has a manufacturing process which can be performed in the ME department machine shop, or outsourced for a reasonable fee (<$500 per component, assuming 1-3 outsourced components).

## Design Challenges

The team's primary design challenges are isolating the LOX fuel from reactive materials, such as the structural Carbon Fiber layers, and maintaining a seal at room-temperature, as well as at cryogenic, operational temperatures.

## Outcomes

The team has developed a tank design that takes the current PSAS airframe design and incorporates a LOX-compatable PTFE liner to chemically insulate the tank from LOX and shrink-fit aluminum end-caps to mechanically seal the LOX off from the rest of the airframe structure at room and cryogenic temperatures.

Tank representation

The following image shows an exploded view of our current tank design.

layer representation

Testing is currently underway to ascertain the material properties of the PTFE, in order to create a more accurate FEA model of the tank and allow for optimization of design geometry.

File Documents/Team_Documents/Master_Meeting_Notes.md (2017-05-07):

#2017-04-27 

**Results from last week’s workflow:**

Chris:  Gasket markdown procedure pushed, CAD Readme started, modified gasket mocked up, just needs to be cut, templates will be cut as soon as acrylic arrives.

Weldon:  Beginnings of procedure template started, brought it up to his work contact, sounds like she is willing to read through things/help approve the process/template to make it more professional.  Still needs to tolerance shrink fit designs

Alex: Sealant arrived, did some endcap/ring shrink fit calcs, ordering etc..

Francesca: Git updated, analysis converted to jupyter notebook, outside testing places contacted

Russell:  Need a bit more time on shrink fit calcs, shrink fit CAD (it is "finalized", has floating dimensions, how much you intend to compress liner, & how much to interfere Al parts)...added delta of compression to the PTFE in the layout sketch. Russell will be running comparison calcs against alex’s

Neil: FEA (modeled 6 ply 0,90,-90 CF epoxy tube with 4000N static loading on one side to begin flight sims, deformation in the .001" range), documentation/organization

**Discussion:**

-Are we going to etch these PTFE tubes?

  -leaning towards maybe etching 2? And incorporating an etched design into a flat end cap, like our very first design iteration, so we have something to try f the sheet liner fails

 ETCH 2 

	-CAD is done already, need STEP file or part file sent off to protolabs to get ordered/quoted

	-means when tubes get here we need to get them turned around and sent off for etching ASAP

	-Chris is getting ball rolling on etching

	-Shear analysis needs to be completed on adhesive surface in general (peeling tension)

-Still need to figure out bridge material/method for sheet design, mats we have may not work

-Add keyway to shrinkfit design to get stuff lined up?

  -this will be dependent likely on experiments below:

-Russell is emailing prof at PCC to see if we can use their laser extensometer(?) for measuring strain of shrinkfit stuff, measuring diamater of cap etc accurately

-Machine faux endcap/ring to test shrink fitting (Fri morning?)

  -Get model made and sent to Mike to see how toleranced it can be on the CNC

-Additionally, try turning down PTFE tube on lathe this day (4/28)

  -Probably worth trying to investigate if it is possible to turn down ourselves

  -Will need to get ahold of LN2 for shrink testing with faux rings etc

  -Need LN2 receptacle for submersion purposes

-Cut our own rings/ptfe and submerge in LN2 and measure ourselves? (per Chris, would like to run this experiment to determine our own coefficients to compare to research)

-Bag Design?

  -Let’s go ahead and investigate this

-Final report lead:Neil/weldon/francesca?

-Need to discuss shrink fit design(done)

**Task designation/discussion:**

*Since no meeting with Dr Jiao this week, let’s go ahead and do this preliminarily today so that Friday can be a workflow day.*

Prelim tasks (pending discussion):

  -More FEA (Neil/Alex/francesca)(ck)

	-Thermal strain hand calcs @ adhesive interface (alex/russell)(ck)

	-Start final report formatting/outline/info: Need final report lead: (neil/weldon?)(ck)

	  -develop & talk to gerry + dr jiao to see if it is in-line with what they want

	-Material properties workbook so it is all in one place and we don’t have to reference stuff in multiple locations (alex has started this already) (done, please update as we go)

	-Ring machining capability in house, with Al stock we already have on CNC?(chris/weldon) (will be decided tomorrow)(ck)

	  -likely will need like 30 min of CAD (russell) to alter design to make it more just a flat top ring, the going into the shop with Kris to get it done on mastercam

		-Shrink fit cap will likely be basically same geometry

	-Develop outline/documentation procedure for Layup (weldon/neil?)(ck) weldon should have talked with his work contact already at this point

	-Prep experimental procedure/documentation etc for hydro/ln2 testing on layups so this is more a fill in the blank process (francesca has a test excel doc)(weldon) (should be done before end of weekend)(ck)

-Drawings out for CAD stuff as well to be sent to protolabs (Russell)(ck)

-prepping layup procedures, gaskets cut, templates cut (chris)(ck)

-bridge design on how to hold it, pop can?  Needs investigation for layup (chris)(ck)

-clean up CAD naming scheme, rename CAD folders to be inline with part folders etc (chris./russell)(ck)

-additional analysis if required (russell)(ck)

-Francesca: documentation.fea,coupon tester guys, jupyter notebook (ck)

*If parts get here:*

	LAYUPS:

   -2 layup squads?

  	-if parts here, likely to at LEAST 1 layup on thurs or fri to start accelerating the timeline

# **2017-04-16**

Updates:  What’d we get done this week?

* CAD finalized (for the time being), Technical drawings completed
	* FEA Full modeling process started (Meeting with John/Ian) (Neil/Alex/Francesca)
		* Further contact from Ian regarding analyzing buckling of composites (this is probably beyond the scope of this project), try to learn as much as we can about the weave, core, elastic modulus, & try to define the sandwich as a whole as opposed to each individual layer.
	* Potential Sealant found (Per Russell)
	https://www.wrmeadows.com/poly-jet-lox-low-modulus-joint-sealant/
	* Chris is setting up a time w/ MELT to do PTFE laser cutting test
	* Contacted Masterbond (adhesive is expensive), Jupyter notebook tutorial started/pushed to git,
	* What Weldon accomplished this week: (started collecting eqns for stress analysis on flat plate end cap) (basically just prep work & some minor analysis at this point so far)
		* Weldon has FE exam this week so some of this time will be committed to that

Part numbering convention:
####-A (first two digits are type of part, i.e. rings or end cap...etc, last two digits are iteration #)
* Liner: 01 series          Example: 0101 is first liner iteration, 0102 is second liner iteration
* Rings: 02 series
* End cap: 03 series
* Al Tape: 04 series
* PRV pipe: 05
* Gasket: 06
	Letters refer to various versions, such as tube liner vs sheet with seam liner
Example: 0201-A is ring designed for sheet liner iteration 1, 0201-B is ring designed for tube liner iteration 2.

> A=Sheet liner, B=Tube liner

**Thoughts:**  
 
* 2nd iteration ring designs?  Pretty good idea, let’s start to analyze for 2nd iteration of ring designs.  This design would alleviate any Etching concerns as it could be accomplished with virgin PTFE + additional gasket.
 
* How do we show a FS=2 empirically for this tank, or on sealant?  We will have to break a lot of tanks….

* Previous teams’ book as a reference..(now around our work area)  they did a TON of work on the airframe stuff, there is likely a lot of data we can simply reference to speed things along

* Focusing on the procedure being scalable is a good idea.  Even though we do not know for certain what the scaled up model will be, we can just choose something arbitrary (aka 10”) so show that things will scale down the line.

For next week: (....) designation afterwards for my purposes only ~NB
	
  * Start researching LOX compatibility more thoroughly (pushed)
	
  * Being FEA full modeling (Neil/Alex/Francesca?) (pushed)
	
  * Order caulking/sealant/permabond this week (ig)
	
  * Order some of those teflon bags to investigate if it will be feasible to include (ig)
	
  * Send off designs/drawings to be machined (1 or 2 replicates?) to begin stage 1 prototyping.  Stage 1 will help us develop the layup procedure for this tank (which is one of the major deliverables for PSAS) as well as providing us with burst test data. (Chris/Weldon) (ig)
	
  * Drawings of 0201A and 0201B will be finalized before 5pm tomorrow (4/17) (Chris)(ig)
	
  * We need to get our hands on LOX and start doing compatibility testing….developing testing procedures/what test? (Need to go to liquid test stand meetings since they are really close to getting some LOX)(If nothing else, let’s get regular contact with them to make sure they can order enough for us to be able to use) (pushed)
	
  * coupled with obtaining LOX, we need to develop what tests we want to do with it, as well as procedures/safety etc regarding LOX testing….(pushed)
	
  * worried about LOX ignition, and oxidation
	
  * Testing etched surface in contact with LOX to see if there is any chemical incompatibility
	
  * Further refine heat transfer analysis (Alex/Russell)(pushed)
	
  * Prelim gasket stress analysis (Russell is waiting on that gasket book, won’t be here for another 5 days or so) (Russell)(solved)
	
  * For all analysis, start moving towards converting to Jupyter Notebook (per Francescas tutorial stuff on git/drive)
	
  * Chris is setting up time w/ MELT for PTFE test laser cutting, as well investigating what scrap acrylic is around for cutting templates.  If nothing else, can go to TAP plastics and just buy some(pushed)
	
  * Consider using  keg ball-lock connector/fitting, keep on back burner for now we will investigate more later (pushed)
	
  * Schedule another LN2 testing time for perform further tests (pushed)
	
  * Literature research party, literary research for composite material
	
  * Start experimental lab write up documentation procedure(from last weeks list)(pushed)
	
  * Spray on chemical insulation research (from last weeks list)(pushed)
	
  * Convert all of these ‘tasks’ to the issues tab on Git, & keep converting everything to Git (Neil)(done)
	
  * Potentially start working on 2nd iteration ring/endcap design (Russell)(pushed)
	
  * Are there any additional things we need to consider/develop for hydrotesting?

** Task focus: **

  Russell- Ht xfer/gasket analysis, then CAD (pushed)

  Alex- Ordering, Heat xfer refinement (pushed)

  Weldon-Stress analysis started last week (FE is on wed, so likely will not be accomplished until wed/thurs) (pushed)

  Chris-Finish drawings/get sent off, get MELT stuff arranged (pushed)
	
  Francesca-LOX compatibility research/cals, transport theory (pushed)
	
  Neil- Git,  get FEA started, manage stuff, help out with analysis etc (pushed)

# **2017-04-09**

Thermal Cycling experiment completed on Fri 17/04/07
	-No visible delamination or issues after submitting test coupons to 1/3/5 full thermal cycles.  All seemed to hold up well, if possible would like to generate more (more than simply 3 preferably to get some actual statistical data) coupons to run either another thermal cycling with LN2 or LOX if possible.
	-Old module frame from crush test was also submitted to Thermal Cycling, this was submerged for ~10-15min, and the ring/module/adhesive all held up very well when submitted to LN2.  Results promising, again, no visible delamination/damage/etc.

Alex made contact with Robert Watzlovick (Guy from that website who did the DIY rocket that we went over in a meeting with Dr Jiao)
-He said his LOX tank failed at cryo temps, we will maintain contact as he was interested in our project.

Problems:  Let’s make a list, as per suggestion by Gerry.
-Obtaining Liner (in general).  Get sheet/tubes here to be worked
-Etching is dangerous! (http://www.plasticsmag.com/features.asp?fIssue=jul/aug-01&aid=3284)
-Budget: need to spend all of it.  Order more stuff, maybe order stuff for EFS if they need anything?
-Machining endcaps/rings, in house/sending off designs
-More stress analysis/calculations
-PTFE machining, PTFE problems...Effing PTFE….
-How do we machine our gaskets?
-Where can we get LOX? Can someone help us with this test? Where do we test?
-How do we perform stress analysis on the composite layers? (contact Ian Zabel)
-FACTOR OF SAFETY OF AT LEAST 2.0 (COLLECTIVE) + calcs to back up
-PRV/Fittings for end caps
-..

PTFE Machinability, how do we go about it?  Create matrix and figure out our BEST working 
option so that we can make the best possible decision to move forward with (as per suggestion by Erin)
Let’s iteratively work on this for a week or since we are waiting on the stupid tubes/rods anyway, and we are at least running tests with a bridge design using PTFE sheet instead.  The matrix for analysis on the BEST possible method is on drive, so if we can formulate the matrix and then sit down and smash through it here in the next week or so that’d be great.  This is in order to determine the BEST possible option of how to machine or turn down PTFE to a thickness/workable form that we want, rather than just moving forward with something that we think “yea this will probably work” & screwing ourselves.

What else can we accomplish this week?  What other decisions need to be made?

-Alternate adhesive -> HYPERLINK "http://www.masterbond.com/articles/applications-research-labs-and-commercial-use-ep21tcht-1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"ep21tcht-1
Recommended by Masterbond given our application (data sheet in materials folder) 
 	-Will call Monday (Francesca) to request sample adhesive.

-Getting designs sent off to be machined
-Need to get this done by Wed 17/04/12.  Let’s get rings/endcaps moving forward.

Liner
-Layup procedure with sheet as opposed to PTFE tube
	-Bridge design idea or try to chamfer ptfe and adhere PTFE to PTFE?  Likely would need a self etching we could do here to accomplish the latter.

-Investigating DIY PTFE etching procedure to save time
	-Bonding primer/adhesive
	http://www.permabond.com/2015/06/10/bonding-ptfe-industrial-adhesive/
	-Customizable teflon bonding kit
	http://reltekllc.com/productlist/teflonbondingkit.aspx

-Etch 3-4 ptfe tubes when they arrive in 2 weeks 

-TO DO THIS WEEK:  Order Permabond alternate etching and some virgin PTFE sheet (even just janky samples) to perform this ‘in house’ etching/adhesion

CAD (Russell/Me(Neil), think you can jump on this and try and get it done by midweek?)
- We need to finish CAD and send it off to a machine shop
-CHANGES: Offset portion, we do not need to have the offset on the lapping portion with a PTFE bridge design, can revert to the previous airframe ring design (ish)
-BRIDGE DESIGN:  Needs to be finalized.  A few different options are available, over/under design? How to adhere? Etc..

Machining
-Gaskets need to get machined.
-Designs sent off, practice machining in house.

Looking forward

-I’d like to get our first layup done here in 1.5-2 weeks.  This means getting designs sent off, gaskets fabricated, hardware ordered (if changed), valves figured out, & a PTFE sheet mounting method finalized to try (if we want to do a layup with PTFE in it, otherwise we can do one without and do a burst test just on the CF tank layup.

-Perform stress analysis on endcap/fasteners/rings.  Likely should do FEA & back of the envelope calculations to try and nail down factor of safety of at least 2 (per PSAS)
-Meeting with Erin/Andrew on Thursday 17/04/13 @ 1pm after our meeting with Dr Jiao, in the LiD.  Erin will be walking us through a markdown format procedure for GIT. We will also discuss purchasing additional material that PSAS can use after our project is over. As well, we can take care of that first assignment for Gerry since we have to meet with our sponsor and write something up, so we need to prep that.  
-Additionally, need to finalize a few items to give to PSAS for the leadership meeting on wed 17/04/12 so they can present some of the stuff we are doing.

-We still have a substantial budget.  We need to spend ALL OF IT.  Start ordering/organizing/thinking about additional/extra materials etc to burn through this remaining budget.  Maybe even can order stuff for EFS team if they need something.

TASKS
-Neil/Russell-CAD (done)
-Neil - Prelim FEA on endcap stress analysis, Experimental write ups for past/future experiments (need proper documentation) (doneish)
-Alex -Ordering many things/Al Sheet for endcaps & test coupons, getting the ball rolling on sending designs off to be machined so it’s ready to go come CAD finalization, lab write up for thermal cycling of coupons (nearly done)
-Chris - emailing MELT to see if they are comfortable lasering PTFE, as well acrylic template for cutting for layups, formal quotes for PTFE etching, PTFE gasket machining (done)
-Weldon - back of the envelope stress analysis calcs for flat endcap/bolt sizing (???)
-Francesca - Heal up, can help Neil with FEA, talk about what else to get done during meeting tomorrow (Monday 17/10/04 with Neil/Russell) Convert current analysis to Jupyter notebooks, setup Jupyter/Git tutorial - transition to Git as primary team storage mechanism.Contact masterbond for sample adhesive. Research sprayon chemical insullation. (mostly done)

# **2017-04-03**

-Set date for thermal cycling of test coupons T7.1-T7.3, Friday? Earlier if possible?
	-Friday before 4pm, let’s get this arranged

-Release valve/adhesive results from last week, which do we move forward with/get ordered.
	-Waiting on quote about adhesive, seems interesting let’s try and move forward

-What else still needs to be ordered?  Need to get everything on it’s way.
	-Returning heat gun accessories 
	-Machine time quotes w/ CAD designs

-CAD updated/machine shop found?
	-Alex found machine shop that seems feasible, for both metal and plastics, let’s move on this

-Prep items/discussion for assumed Thurs meeting with Dr Jiao.  Likely show test coupons, discuss what has been ordered, show faux tensile testing experiment from finals week etc.
	-Do we need to reserve room for this timeslot again? As well we need to check with Dr Jiao if 12pm still works for her this term.
	-Room already reserved, good to go

-Beginning of “down time” where we are waiting for parts, what can we accomplish? Machine shop work on rings/end caps?

-Other topics/concerns?

Additional topics to take care of:

-Talk to Mike about boring out PTFE

Chris: PTFE- if quotes come in at same time, get from both vendors
	-OD:3”

# **2017-03-27**

Need to set date/time, how about Sunday @ 6pm, or Monday @ 6pm?

This agenda serves as a guide/preliminary decision making prior to the meeting, just to get all of us thinking about what needs to be done so that we can finalize and move forward during our meeting here in the next few days.

There are a few items/decisions that need to be finalized, as well, we need to move forward asap to the prototyping stage.

Ordering:  We need to get things ordered ASAP.  With this term coming to a close, and lead times stacking up, we need to get everything that we need ordered and on it’s way.  Hopefully we can get everything finalized and ordered by the end of the week, 3/31/17.  Preferably, we need to order enough key items so that when things arrive in 2-3 weeks we can construct at minimum 2 or 3 prototypes for testing. With how much time we have left coupled with lead times for all of these materials/parts, if something needs to be changed we will likely only have time for 1 iteration if we only order enough for 1 or 2 prototypes at a time.  Things that still need to be ordered with extensive lead times are as follows:

	-Nomex
	-PTFE
	-Teflon bag liner(http://www.welchfluorocarbon.com/custom-manufacturing/heat-sealing/)
	-Aluminum for in house machining
	-Mating Rings
	-Endcaps
	-Additional fasteners/fittings for hydro testing
	-???

In regards to the list above, we can move on to a few discussion items/decisions as detailed below.

Mating Rings, Endcaps, In-House Machining

In-House Machining:  I do believe this is a good idea for the low cost, open source nature of this project.  However, there will be a fairly steep learning curve as none of us have extensive machining experience, not to mention we will need to arrange time with Mike/others in the machine shop to show us everything/supervise etc.  As well, we are working within some tight tolerances so there will definitely have to be some practice involved.  It has been discussed between a few of us already that we may want to lean towards sending off designs to a local shop to have them do it for us.  I propose that we do both.  Since lead times are involved, I propose we send off designs to a machine shop (minimum 2 replicates so we can construct at least 2 prototypes) to be professionally machined.  This is so at the very least we will be able to have in our possession rings/caps that WILL work within our tolerances.  This will require CAD models being finalized/drawings created by early in the week so that we can get quotes and send off to a shop.  Since this will likely involve at least a week or 2 lead time, we can get ahold of aluminum and use this time to try and beat the learning curve in the machine shop and practice fabricating pieces ourselves.  

Name Agree Disagree Comments  
 
Neil +    
 
Russell +    
 
Alex +    
 
Francesca +    
 
Chris +    
 
Weldon     

Mating Rings:  These designs are nearly final, though with Alex discovering the Teflon Heat Liner ( http://www.welchfluorocarbon.com/custom-manufacturing/heat-sealing/), it makes me think this may in fact be a cheaper and quicker option than the PTFE, while still achieving the same desired effect & quality of tank.  If we elect to use this ‘teflon bag’, it means that the ring designs will change slightly.  As mentioned above, I think we could in fact do both, especially if we send off designs to a machine shop.  We will just have them fab the 2 different designs, and we can compare layup procedures/effectiveness of each if we construct both models.  This can also be accomplished by us in the machine shop while we are waiting on lead times.  These are the designs that I am thinking of:

 (1) Same PTFE design with offset lapping portion to allow PTFE to be inner layer of the tank:

(2) Alternate design for Teflon Bag, with no offset portion, similar to below:

Using this secondary design with a teflon bag, we could even potentially ‘double line’ the interior, incorporating one layer into a layup, and then lining the inside of the tank a second time post curing process.

Name Agree Disagree Comments  
 
Neil +    
 
Russell +  I think we exhaust the liner possibilities before giving up and moving to the bag. I think there is a possibility that we can lay up onto a thicker tube, then bore it out afterward with the challenge of getting a good surface finish.  
 
Alex +  Our current liner design is the better option, but at least the bag can serve as a backup.  
 
Francesca +  ^This^  
 
Chris +    
 
Weldon     

End Caps:  As discussed preliminarily between a few of us, I think the end cap design can be simplified to just a flat plate design.  Under our operating pressures having a curved geometry for an end cap is likely unnecessary, as the stress concentrations will be occurring at the joining interface and fasteners of the tank.  Not to mention a flat end cap would be much easier to machine, both in house and by a machine shop.  We could move forward with this alteration of a design for at least the initial prototyping stage, and if it appears that we need to alter them back to a curved geometry then we have that possibility. 

Name Agree Disagree Comments  
 
Neil +    
 
Russell +  What Francesca said, but we can always use a nipple with gaskets and nuts, which won’t handle as much pressure, but may handle enough  
 
Alex +    
 
Francesca +  If we are doing a flat plate, I think we should consider shaving down a thicker plate to allow for a thin wall with a thicker center-section that can be tapped through and used to mount inlet/release valves  
 
Chris +    
 
Weldon     

Additional Considerations:  If we can get everything ordered and underway, we will have a couple weeks of just waiting around for things to get here.  During this time, as mentioned above we can work in the machine shop, but as well work on acquiring additional necessary resources, as well as performing tests.  More coupons can be created for thermal cycling, which means we can find a source of liquid nitrogen for said testing (hopefully from the PSU chem department for ease of access), as well as methodology and a location to be able to perform these tests.  Also, if we can get a sample of the teflon bag in our possession rather quickly it would be nice to run a set of coupons using this material as we have with the PTFE to see how it holds up against METLBOND and the CF curing procedure.

Adhesive:  Need to look into backup adhesive (do some research into company Masterbond), in case METLBOND isn’t going to cut it..

DECISIONS:

-Move forward with Flat End Cap
-Move forward with 0.25” wall thickness PTFE, 3” ID, with etching, get quote, get it rdy to order asap (5 replicates)
-Fab 2 designs, one for teflon bag, one current design

# **2017-03-09**
--------------------------------------------------------------------
**Progress**

On 3/5 we did some test layups with the virgin side of PTFE to assess the melt bond’s ability to adhere.

One PTFE on aluminium

One PTFE on carbon fiber

One PTFE on nomex

Additional test measurements on the shrink tape

**Updates **

*(short statement of results we can talk about process after the meeting if anyone has questions)*

Additional test measurements on the shrink tape (needs to be re-done, failure during heating process)

All adhesive failed on virgin side as expected

Erin want’s us to to 3 inch

He wants us to go simple with caps

We will have to explain to Gerry that are design considerations are being shortened.

**Weldon**

**Francesca**

**Neil**

Concerns with METLBOND 1515 & LOX

*From Metlbond Data Sheet… see meeting_notes/media/media folder for image01*

Would like to run simple test with coupons + metlbond asap, (ex submerging in small amount of LOX) to test degradation/speed of potential failure...may not have immediate effect and will work out OK

**Russell**

**Chris**

**Alex **

Got budget done. Let’s start spending money.

No overhead taken out of the award

Check the units on the ipython notebook optimization

[*www.Watzlavick.com/robert/rocket/rocket1*](http://www.watzlavick.com/robert/rocket/rocket1)

**Whats Next?**

(Time to make decisions on what we need to do next week)

# **2017-03-02**
---------------------------------------------------------------------------

**Progress**

On 2/26 we did some test layups with the chemical etched PTFE to assess the melt bond’s ability to adhere.

One PTFE on aluminium

One PTFE on carbon fiber

One PTFE on nomex

We also did some preliminary test measurements on the shrink tape

**Updates **

(short statement of results we can talk about process after the meeting if anyone has questions)

Weldon

I’ve been sick most of the week, and haven’t made much progress. I should have the notes from the safety training up in the next couple hours. I’m also putting the finishing touches on the documentation procedures. I’ve been gathering safety documentation as well. I’m also trying to gather documentation on standard LOX tanks and filling procedures.

Francesca

Neil

Russell

Chris

Alex

**Whats Next?**

(Time to make decisions on what we need to do next week)

#**2017-02-23**
--------------------------------------------------------------

**Progress**

**What we said we would do**

Alex- Weight reduction on cad models, follow up on contacts for quotes on donations

Russell- More research on PTFE, Spend some time looking at strength and permeability.

What is the pressure from shrink tape?

Baseline thickness of PTFE liner

Weldon- going to chem safety training contact gas suppliers, put together a documentation standard

Neil- FEA heat transfer analysis

Francesca- FEA play around with different materials , abstract for AIAA, meeting tuesday about python.

Chris - Get quotes for PTFE liner, What kind of surface treatment do we use, Continue to move things to github and make issues.

**Alex**

**What did you do?**

Looked at aluminum suppliers and possible endcap manufacturing options.

**What do you need?**

Get together and talk about design

**Whats next?**

Send budget to jun

**Chris**

**What did you do?**

We have samples!

Requested quotes from APT and these guys.

[*http://catalog.fluoropolymerproducts.com/viewitems/all-categories-molded-teflon-cylinders/ries-molded-teflon-cylinders-molded-ptfe-cylinders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*](http://catalog.fluoropolymerproducts.com/viewitems/all-categories-molded-teflon-cylinders/ries-molded-teflon-cylinders-molded-ptfe-cylinders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)

[*http://www.enflo.com/products/molded-ptfe-cylinders/*](http://www.enflo.com/products/molded-ptfe-cylinders/)

[*http://technetics.com/products/ptfe-polymer-solutions/ptfe-shapes/rod-and-cylinders/*](http://technetics.com/products/ptfe-polymer-solutions/ptfe-shapes/rod-and-cylinders/)

**What do you need?**

**Whats next?**

**Call enflo about Molded PTFE Cylinders (1-713-983-4201)**

**Neil**

**What did you do?**

[***https://drive.google.com/open?id=0B26o6W76DxOec291OEVBQlhRY0k***](https://drive.google.com/open?id=0B26o6W76DxOec291OEVBQlhRY0k)

Made SS thermal stress FEA

Deflection as a result of cryo cooling

Found out how to move solid models to abacus

Worked on AIAA abstract

**What do you need?**

Solid models

**Whats next?**

Vibrations?

**Francesca**

**What did you do?**

Working on AIAA

**What do you need?**

**Whats next?**

**Russell**

**What did you do?**

Sizing for the thickness of liner

Back of envelope calculations based on a 1mm material thickness.

6\*7\*.04 cylinder is about .41 lbs

Permeability 5.86cm^2 O2 lost per hour (possibly not an issue)

Yield strength of PTFE about 182 psi at 175 c (from linear interpolation)

> Max pressure on cylinder is about 2.4 psi (we won’t be able to layup on this)

Insulation properties (not great at the thickness we are looking at)

> [*https://drive.google.com/open?id=0B80-Nm0s3cT6VXhIdFNLOGdUNmM*](https://drive.google.com/open?id=0B80-Nm0s3cT6VXhIdFNLOGdUNmM)

Take away

PTFE will only be useful as a LOX barrier. Go as thin as possible!

**What do you need?**

**Whats next?**

**Weldon**

**What did you do?**

I went to the chemical safety training. Some good information there about safety and emergency services. I’m working on writing up a sheet of notes for easy reference.

Started work on a documentation procedure document. Not quite finished yet.

Have been researching LOX suppliers, storage containers, and filling procedures. I’ll put together a sheet about this as well (likely I’ll get this done just after I get the documentation procedure finished up).

**What do you need?**

**What’s next?**

Finish creating the documentation procedure, and follow it while producing note sheets on the safety training and general LOX information.

Follow up on some research concerning regulations and codes associated with the use of LOX as part of the fuel mixture for LV4.

Explore concerns about how long the LOX will remain in it’s liquid state under the current design conditions.

> What issues might need to be addressed if the pressure of the expanding gas exceeds the design pressure?
>
> Would that cause any catastrophic problems in the fuel pump system?

# **2017-02-16**
----------------------------------------------------------------------------
Alex showed off some designs he modeled

Need holes and weight reduction (we still need to refine the thickness)

Now that we have a model we can get a quote for PTFE liner

Indium lining of interface

Do we want to account for insulating materials

> Foam or vacuum
>
> With such a small gap will insulation actually help
>
> Nomex will also help insulate
>
> Let's not worry about it

Limiting factor for aluminum is how thin we can machine it

Thin wall pressure vessel calculations

For the pressure we are going for the an aluminum tank would be very thin

Permiability of O2 through PTFE

What we are looking at is at room temperature

Document everything

Nasa want reports from us

Show them that we are doing things

They want “nuggets”

Test coupons

How are we going to create them ?

What are the specks of the test coupons for testing?

Lab in ondine does not want a bunch of students to using the lab.

Perhaps they will do the testing for us.

This would be great!

It would be great if testing was our least concern

How do we want to test them

Margaret is our contact for money.

Lets buy stuff local if we can and reduce shipping cost

Prototyping

How are we going to load the tank with pressure

Will it seal cold?

Air gas and matheson

Let's talk to them and get some info

Talk to them online

**What will we get done this next week**

Can we find someone to stamp out an aluminum endcap?

What sizes do they have available?

We can then order more than one

Alex- Weight reduction on cad models, follow up on contacts for quotes on donations

Russell- More research on PTFE, Spend some time looking at strength and permeability.

What is the pressure from shrink tape?

Baseline thickness of PTFE liner

Weldon- going to chem safety training contact gas suppliers, put together a

Neil- FEA heat transfer analysis

Francesca- FEA play around with different materials , abstract for AIAA, meeting tuesday about python.

Chris - Get quotes for PTFE liner, What kind of surface treatment do we use, Continue to move things to github and make issues.

# **2017-02-09**
------------------------------------------------------------------
What have we done, what will we do, is there anything holding us back?

[***Action Plan***](https://drive.google.com/open?id=1IFkCph4sUu5lX_zHoPREmssZP85U279T_9PHecbIcHA)

**Contacts**

Made contact with APT Teflon working on getting samples(most likely get them) They may be able to manufacture a liner that we can then layup on top of. (potentially).

Made contact with Jerry from 3M aerospace tapes and adhesives department. Looking into scotch weld. (Haha)

**Modeling**

Has anyone modeled anything yet?

No

**Finances**

We were told by Andrew that if there are more financial concerns they should be directed towards him.

We have to pay for shipping of samples andrew is paying with cc

**Documentation**

GIThub tutorial in the rocket room 1 pm, 2/9

Let’s get some end cap drawings

**Design**

[*https://drive.google.com/open?id=0B\_82kiJ5gcsyR2Eya3JLbmswQUE*](https://drive.google.com/open?id=0B_82kiJ5gcsyR2Eya3JLbmswQUE)

-Arbitrary tank design dimensions: **4’’ inside diameter, 8-¾’’ inside long** or 6’’ diameter, 13 inch long

-**Tank working pressure around 3 atm**

-Pump team is optimizing pump to work with tank pressure between 2 - 3 atm

- Timeline to complete design phase in 6 weeks

What do we need to accomplish?

Who is going to accomplish these tasks?

-we may need a thermal buffer at the ends

-what kind of shape

With regards to thermal coefficient (show in our design that we are considering this)

How much will the hemisphere contact

> **Timeline**

16 weeks to get everything done

Iteration every 2 weeks. By the third iteration hopefully we will nail down our design 2/16

When we send thing to manufacturing we will plan what we will do while we wait

**Presentation **

Problem 1: thermal expansion diff (Francesca)

Problem2 : How do we manufacture (interfacing and manufacturing)

If we can just layup everything in one piece (Neil)

Problem 3: seal (Weldon)

**Meeting With Jun**

We have leveraging for money

Too many tests can be a waste of our time

We should be confident with our design

Lets only do meaningful tests

Do we have potential vendors

Machine science( has helped PSAS)

ProtoLabs

Check Ebay or alternative sources (can we recycle things?)

Can we find a teflon tube somewhere else

**Things to do**

1.  Presentation slides: Neil, Francesca, Weldon

2.  Team Contract Revision: Chris, Russell, Alex

3.  Test meltbond

Test every one of our interfaces individually

-machine shop to cut Al

(alex will come in tomorrow)

-Layup on Sunday: Alex, Francesca, Neil, Chris

9 Am

4) FEA Donut thermal analysis: Neil, Francesca

5) Design Options: decision made during 2/16 meeting

#**2017-02-02**
-------------------------------------------
-   We meet trishia

    -   Requirements for OSGS

    -   We need to come up with the matching funds

    -   Alex has been great

    -   She has concerns with the budget

        -   We were awarded 8000 trisha thought we needed to raise 24,000

        -   We clarified that we have a bunch of donated materials

        -   Maybe get a contract from psas

        -   We purchase through psas for the 2000

        -   **We need to talk to andrew (get a contract for $2136)**

        -   **We need to make trisha’s job easier**

            -   Trisha has less worried now

        -   **No spending OSGS funds yet**

        -   Is someone going to take a cut out of our money?

            -   Subcontract

            -   Overhead

            -   We may see less than 8,900

            -   Probably 5%

            -   We need to be very careful with spending and documentation to make the university and NASA happy

            -   Boeing has was compensated last year for their donation

            -   Make lasting relationships and good connections to open bridges and keep them up.

    -   Team roles

        -   We need to come up with a way to evaluate members

        -   Let’s get rolling on this 16 weeks left

    -   What should jun expect next week

        -   We are doing a layup on sunday 9AM

        -   **We should meet more.**

        -   Do we want to make Gerry happy or PSAS

            -   Making gerry happy will fall in

        -   Make a plan for who will do what

        -   Not everyone needs to do everything

    -   Action plan

        -   We have a list of tasks that we need to do lets divide the tasks by subteams.

    -   Jun’s question

        -   Do we want to look into professional manufactures with the money we have?

        -   Then maybe we could compare what we have

        -   This is not an option for our final deliverable

    -   Jun’s research

        -   Liquid nitrogen is colder

            -   **We need a way to test for micro diffusion**

            -   There are still safety concerns with LN

    -   **We should reach out to companies that are already making tanks (LOX and nitrogen and also composite tanks.**

#**2017-01-26 Meeting with jun**
----------------------------------------------
-   Jun’s said some things

    -   We are ahead of most groups

    -   Has contacts we might be able to use for materials

        -   They have already helped PSAS once let's convince them to do it again.

        -   If you can’t supply materials can we talk to someone who was apart of the project with NASA

-   Presentation

    -   Jun’s comments

        -   How do we measure the pressure

            -   Russell has a plan using his own equipment

        -   Test one at a time and improve from that until the fabrication is perfected

            -   Alex “we can practice layup procedure”

        -   So prototype?

        -   Safety committee we need to notify someone

            -   She said that she can do it

            -   Can we bring samples somewhere to test?

        -   Jun likes the idea of letting professionals handle the LOX

        -   PAy attention to how much epoxy we use (maybe less is more)

        -   Add more to the reading list. (EXPAND the list)

        -   We can tour her lab any time

            -   (Next Tuesday)

        -   Record everything we do every time we layup( time, temp amount of epox, etc.)

            -   Change one thing at a time

            -   Have a methodical way of laying up

    <!-- -->

    -   Other things about presentation

        -   Epoxy is reactive

        -   Material selection has been done by erin (PTFE is ideal place to start)

            -   We might be able to get someone to machine for us

        -   Stuck with aluminum endcaps.

        -   Tank inside the module is not what erin wants. We make the module the tank.

        -   Opt program has given us dimensions

        -   We may share LOX resource with other PSAS team

        -   Thin aluminum liner(back up)

        -   Sketch tank design for a week Starting today!

        -   Add layup challenges to GANNT

<!-- -->

-   We talked about lab space

    -   Laser fire

    -   We need to be able to have access to the room

# **2017-01-12**
-------------------------------------------------------
>
> First meeting with Professor Jun Jiao.
>
> Main topic: Oregon Space Grant Consortium project proposal.
>
> -Quantify 2:1 funding from PSAS crowdfunding donations.
>
> -Emphasize that we are building off of a previous capstone and we have available resources and support.
>
> -Define clear team member roles
>
> -Provide team member info to show that we are an impressive group
>
> *1/11/2017 12:00 PM -- Google Hangout Meeting with Alex, Joseph, Russell, and Francesca*
>
> OSGC Proposal
>
> Discussed how to move forward with OSGC proposal:

-   We will be sticking with Jun Jiao as Advisor - Alex is emailing her, providing her with additional information so she can complete her letter before Friday. Probably no meeting due to snow - we are offering to meet via video chat tomorrow (Thursday, the 12th)

<!-- -->

-   Trying to model our proposal after fuel pump team’s - Alex is emailing them to see if they will allow us to look at their draft.

<!-- -->

-   Still waiting on email response from Andrew with clarifying questions about proposal (matching funds, etc).

<!-- -->

-   Russell is taking lead in researching materials and quotes to add to BOM - anyone with time to do so should try and contribute to BOM.

<!-- -->

-   Agreed to ‘meet’ up again at 9PM to discuss progress.

> Contacts: contact sheet added by Alex to drive- everyone should add their email and phone \#
>
> Reminder: Please add weekly availability to ‘availability’ doc, if you haven’t already.
>
# *2017-01-05**
>
> Oregon Space Grant Paper
>
> http://spacegrant.oregonstate.edu/student-research-projects
>
> -We need to start writing (due Jan. 13)
>
> -We need to come up budget
>
> -materials
>
> -AIAA registration
>
> -Faculty support options
>
> -Gerry
>
> -Weislogel
>
> -Raul Cal
>
> -Andrew (if necessary)
>
> -Wern
>
> We should write the faculty support letter.
>
> Material
>
> Find pricing for liner test materials:
>
> -PTFE
>
> -ETFE
>
> -PET
>
> -cryogel as an insulation layer/barrier
>
> -We can create test strips to test adhesion
>
> Design
>
> We have to figure out an endcap design
>
> -does it depend on the material we select
>
> Schedules
>
> -Enter winter term weekly schedule into google sheet
>
# **2016-11-15**
------------------------------------------------------------
> Rocket Capstone
>
> Target altitude of 100km
>
> Build a hobby rocket that will go to space
>
> Rocket equation V=Veln(mo/mf)
>
> Tank Prototype

-   Small scale test tank that demonstrates the design

-   Not responsible for plumbing

    -   There is help available

    -   We do need a fill valve and purge valve

    -   Machine endcaps with gasket

-   We have an idea

    -   On diameter (about 10”)

    -   Flow rate

    -   Volumes

-   Rocket equation V=Veln(mo/mf)

    -   The only change in mass is in the tank

-   Without the fuel pump we would need about 700 psi

    -   Shoot for at least 50 psi (more is better)

-   End caps do not need to be a composite

    -   Bolted on maybe, or something else any ideas?

-   Low tech

-   Composites are stronger and lighter

-   Hydrotesting will need to be done

-   We will also need to do a cryo fill

    -   We can observe the behavior of our lining and its interaction with the composites

-   Internal geometry

    -   Baffles

        -   Slosh

        -   Vortex

-   Make lots of prototypes and test them

-   Lots of materials properties data has been collected

-   We want a 2.5 factor of safety

    -   We will need to estimate the in flight loading

> BIG PROBLEMS

-   Epoxy is not LOX safe

    -   We will need some sort of liner

        -   No diffusion or leaks or bad things will happen

        -   Watch the interfaces for leaks

-   Account for thermal contraction and expansion

    -   Perhaps have a slightly larger liner than shell to allow for shink

> Document everything

-   Open source project

-   We want to leave something that future generations can benefit from

> This is not a project for someone who wants an easy one. Lots of time will need to be put into this
>
> Neil *NAB2@pdx.edu*
>
> Francesca *FF2@pdx.edu*
>
> Michael *mboyles@pdx.edu*
>
> Jonathan *balogh@pdx.edu*
>
> Musallam *alzamel@pdx.edu*õ

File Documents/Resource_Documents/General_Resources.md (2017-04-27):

**Resources**

Github tutorial

[*https://try.github.io/levels/1/challenges/1*](https://try.github.io/levels/1/challenges/1)

University of Florida’s cryogen safety

[*http://www.ehs.ufl.edu/programs/lab/cryogens/*](http://www.ehs.ufl.edu/programs/lab/cryogens/)

Foam interior/potential other commonly used sandwich materials used with carbon fiber:

[*http://www.fibreglast.com/product/guidelines-for-sandwich-core-materials/Learning\_Center*](http://www.fibreglast.com/product/guidelines-for-sandwich-core-materials/Learning_Center)

Potential Indium resources:

[*http://www.indium.com/engineered-solder-and-alloys/cryogenic-seals/*](http://www.indium.com/engineered-solder-and-alloys/cryogenic-seals/)

[*https://ntrs.nasa.gov/archive/nasa/casi.ntrs.nasa.gov/19890013479.pdf*](https://ntrs.nasa.gov/archive/nasa/casi.ntrs.nasa.gov/19890013479.pdf)

[*http://www.aimspecialty.com/portals/0/files/sealing-with-indium.pdf*](http://www.aimspecialty.com/portals/0/files/sealing-with-indium.pdf)

[*http://www.espimetals.com/index.php/online-catalog/854-indium-foil-sheet*](http://www.espimetals.com/index.php/online-catalog/854-indium-foil-sheet)

Markdown tutorial - coding for .txt files that should help with presentation?

[*http://www.markdowntutorial.com/*](http://www.markdowntutorial.com/)

*Potential Vendors/Resource Contacts*

*MACHINING*

Machine Sciences (Wilsonville)

http://machinesciences.com/

Toll Free: 866.682.9980

Telephone: 503.682.9980

Fax: 503.682.9989

Email: **info@machinesciences.com**

Address: 10165 SW Commerce Circle, G, Wilsonville OR 97070

Advanced Machining Services (Bend)

(Precision Aerospace Components)

[*http://amsbend.com/*](http://amsbend.com/)

Advanced Machining Services LLC

20690 Carmen Loop \#100 - Bend, OR 97702

Tele: 541-617-9500 - Fax: 541-617-7496 - info@amsbend.com

Davis Tools Inc

http://www.davistl.com/index.php/manufacturing/

-   NADCAP Accredited (National Aerospace and Defense Contractors Accreditation Program)

**Davis Tool Inc**

**3740 NW Aloclek Place**

**Hillsboro, OR 97124**

**(503) 648-0936 **

Prigel Machine & Fabrication Inc. (Hood River) (not as hopeful about this one)

http://www.prigelmachine.com/

3895 Heron Drive

Hood River, OR 97031

541-354-1990

*PTFE*

[*http://www.advanced-emc.com/manufacturing-capabilities/*](http://www.advanced-emc.com/manufacturing-capabilities/)

[*http://www.boedeker.com/ptfe\_p.htm?utm\_source=google&utm\_medium=cpc&utm\_campaign=PTFE%20Plastics&utm\_content=ptfe%20tubes&utm\_term=%2Bptfe%20%2Btubes&gclid=CKD1po\_KzNICFYNXfgodf1kNVA*](http://www.boedeker.com/ptfe_p.htm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) (with typical material properties datasheet on website if values for analysis are needed) (*This one likely will not work out, only spec’d down to -73C*)

[*http://www.professionalplastics.com/Teflon\_Tubing*](http://www.professionalplastics.com/Teflon_Tubing) (see link/comment halfway down page, looks like they offer 2” to 20” OD compression molded PTFE tubing) (this place is in Tualatin, probably same place Chris found)

[*http://www.midlandplastics.com/srtd\_PTFE.htm*](http://www.midlandplastics.com/srtd_PTFE.htm) (**Tubing**

Extruded or molded PTFE tubing is available in outer diameter (O.D.) dimensions of 1/16 inch up to 60 inches.) (Sent them email/questionnaire form, waiting to hear back)

[*http://www.nationwideplastics.net/high-performance-plastics/ptfe/*](http://www.nationwideplastics.net/high-performance-plastics/ptfe/)

(Contacted, waiting for response)

[*http://www.houmfg.com/products/machining.php*](http://www.houmfg.com/products/machining.php)

(Contacted,waiting for response. Their website says they do custom PTFE machining and generally work within tight tolerances)

*Aerospace Nomex Honeycomb*

[*http://www.ahtinc.com/products.htm*](http://www.ahtinc.com/products.htm) (previous vendor I believe?) (contacted them for a price quote for 1 sheet (48”x96” hexagonal cells,0.125”-0.25” thickness),waiting to hear back. Assuming 3” ID & 3” height per rough calculations by me & Russell 1 sheet should be plenty of material.)

[*https://www.plascore.com/honeycomb/honeycomb-cores/aramid-fiber/pn2-aramid-fiber-honeycomb/*](https://www.plascore.com/honeycomb/honeycomb-cores/aramid-fiber/pn2-aramid-fiber-honeycomb/) (these guys also do plascore/aluminum honeycombs)

[*http://www.hexcel.com/Products/Honeycomb/HexWeb-Honeycomb*](http://www.hexcel.com/Products/Honeycomb/HexWeb-Honeycomb)

*Hydrostatic Testing Pump*

[*https://www.grainger.com/product/WHEELER-REX-Hydrostatic-Test-Pump-6GDU4?s\_pp=false&picUrl=//static.grainger.com/rp/s/is/image/Grainger/6GDU4\_AS01?$smthumb$*](https://www.grainger.com/product/WHEELER-REX-Hydrostatic-Test-Pump-6GDU4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)

(hand operated,¼” outlet, up to 300 psi)

*Robert Rocket Project*

[*http://watzlavick.com/robert/rocket/*](http://watzlavick.com/robert/rocket/)

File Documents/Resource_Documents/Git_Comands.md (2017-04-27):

**Google how to change notepad to default editor for git**

$ cd

$ cd . (current folder)

$ clear (clears screen)

$ ls (list)

$ls l

$ git status

$ notepad new.txt

$ git add new.txt

$ git commit

i &lt;-insert (type in message)

Esc

:wq (write quit)

First line is for the short message

Skip a line

3rd line start long message

$ git push (will try to push)

$git pull

$git add

Previous directory: $cd ..

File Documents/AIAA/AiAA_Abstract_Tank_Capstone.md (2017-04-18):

*Submission Requirements:*

**Abstract Title (Title Case):** Design and Manufacture of Composite
Liquid Oxygen Propellent Tank for University Rocket

**Presenter Biography (200 Words Max):** Chris Wilson is a Mechanical
Engineering student at Portland State University. He is active with the
Portland State Aerospace Society (PSAS) and involved in their CubeSat
project.

Wilson has managed to maintain a strong GPA, full time status, a job and
a family. Growing up, Wilson watched his father work and maintain
sailboat engines while traveling from one country to another. Observing
his father operate marine diesel engines created a strong understanding
and love of mechanics. He has worked as an emergency medical technician,
volcano tour guide and volunteer firefighter. When he graduates he
aspires to enter the aerospace field and make meaningful contributions
to space travel.

**Presentation Type:** Technical Paper

**3 keywords (min) (Dropdown list):** Aerospace Design and Aerospace
Structures

**Authors:** Neil Benkelman, Russell Berger, Weldon Peterson, Alex
Farias, Francesca Frattaroli, Christopher Wilson

**Topic:** Space Transportation and Launch Systems

> *Supported by the AIAA Space Transportation Technical Committee and
> the AIAA Reusable Launch Vehicle Program Committee*
>
> The commercial, military, scientific, and human exploration of space
> depends upon highly reliable access at reasonable costs. Commercial
> companies have offered the promise of low-cost space access, and some
> are currently developing, testing, and operating their systems. NASA
> has begun operation of low-cost, reliable commercial cargo delivery,
> and is developing crew delivery, to the International Space Station
> (ISS). The NASA Space Launch System (SLS) will provide the Orion
> crewed spacecraft a capability to reach deep space destinations.
> Launch capabilities are also emerging on several fronts to transport
> the increasing number of small satellite payloads to orbit.

-   Emerging launch system designs, concepts, and developments

-   Space transportation technology design, and integration challenges

-   In-space transportation systems and architectures, including
    > propellant depots

-   Launch vehicles and systems (including suborbital)

-   RLV development, programmatic (including economics), and
    > industry-related strategies

-   Lessons learned from previous programs and design studies

-   Space transportation for space tourism

-   Space transportation analytical tools, materials, and technologies

-   Operations of spaceports and ranges

**Please direct questions to: (Space Transportation and Launch Systems
contacts)\
***[Brian Pomeroy\
](mailto:brpomeroy@gmail.com)[Steve Bauer\
](mailto:steven.x.bauer@nasa.gov)[Dave
Masten](mailto:dmasten@masten.aero)*

**Abstract:**

“Each submission must be formatted as an extended abstract with a
minimum of 1000 words, or as a draft manuscript. The submission must
include sufficient detail to demonstrate the purpose of the paper, the
technical foundation for the topics to be discussed, any preliminary
results to date, and the expected results of the final paper, including
key figures, equations, tables, and references, as appropriate.
Sufficient information must be included in the submission to convince
the Forum organizers and reviewers that the author(s) will have a strong
likelihood of completing the final paper by the final manuscript
submission deadline.”

**Design and Manufacture of Liquid Oxygen Propellent Tank for University
Rocket**

1.  **Abstract (of the Abstract):**

    a.  **Goal: Design and documentation of composite LOX rocket tank **

    b.  **Contribution to PSAS mission**

    c.  **Anticipated results**

2.  **Introduction:**

    a.  **objective: replace Al, reduce dry weight, retain necessary
        > strength and chemical non-reactivity**

    b.  **past work/results - airframe, composite tank literature**

    c.  **theoretical background/basis**

    d.  **expected finished product**

3.  **Significance:**

    a.  **reach von karman line**

    b.  **dependent PSAS projects - EFS**

    c.  **advancement of university rocketry**

4.  **Plan of Work:**

    a.  **pre-existing resources/techniques**

    b.  **design methods**

    c.  **test methods**

    d.  **timeline**

    e.  **final product and testing**

Design and Manufacture of Composite Liquid Oxygen Propellent Tank for
University Rocket

**1-Abstract**

When designing a rocket to overcome Earth’s gravitational force, the dry
mass of the propellent tank is the most limiting factor for amateur and
university-level rocket teams. Most rocket groups are dependent upon
heavy aluminum tanks to hold their liquid propellant. Single-piece,
carbon-fiber composite tanks are strong and light, but require expensive
automated fiber placement techniques that are not a viable option for
amateur teams, who operate with a tight budget and limited resources in
comparison to their corporate or government counterparts. Portland State
University’s composite-tank capstone and research project is an attempt
by senior undergraduate engineering students to design, build, and test
an affordable, lightweight, composite liquid oxygen (LOX) propellant
tank for eventual integration into Portland State Aerospace Society’s
100 kilometer rocket.

**2-Introduction**

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

Two previous PSAS capstone groups have focused on improving the overall
dry-weight of the PSAS LV3 rocket, a third generation solid-propellant
rocket. The 2014 and 2016 Airframe capstone teams developed a unique
carbon-fiber composite layup technique[^1], in which layers of carbon
fiber, adhesive, and nomex honeycomb were laid up onto 6-inch aluminum
mating rings, producing 18-inch airframe modules that were then mated
together to form the body of the LV3 rocket. Having significantly
reduced the mass of the rocket in this way, PSAS is seeking to reduce
the mass of the internal components, starting with the propellant tank
module.

**3. Significance:**

Being able to design a working, lightweight, liquid-propellant tank
using resources accessible to a university student organization, will
not only assist the PSAS community in achieving its goal of breaching
100km and exploring high altitude science by putting a cubesat into
orbit, but provide the greater rocket community with a more affordable
and accessible tank design. Due to its nature as an open source project,
all results will be posted publicly, allowing any future university or
amateur team to benefit. Additionally, the financial and technical
constraints of this project also pose an opportunity to develop unique
solutions to the problem of cryotank design that could benefit industry
and science as a whole.

**4-Plan of Work**

The scope of this project builds on the previous work of other student
groups. As previously noted, a 2016 capstone group developed a layup
process and design of a lightweight composite airframe. Investigation
into what techniques, procedures, and materials that can be adapted from
this project are already underway. Additionally, research into composite
cryotank technology,[^2] and associated methods and safety protocols has
already been done before; PSAS has aggregated hundreds of relevant
technical papers and NASA procedural documents which are currently being
evaluated by the design team and are expected to inform initial designs,
material selection, and testing methods.

{width="4.296875546806649in"
height="3.5677088801399823in"}{width="3.682292213473316in"
height="2.0494706911636045in"}

  *Figure 1: NASA/Boeing CCTD Cryotank with Fluted-Core Skirt. Illustration: Karl Reque*   *Figure 2: 2015-2016 Composite PSAS airframe layer configuration*
  ---------------------------------------------------------------------------------------- -------------------------------------------------------------------
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

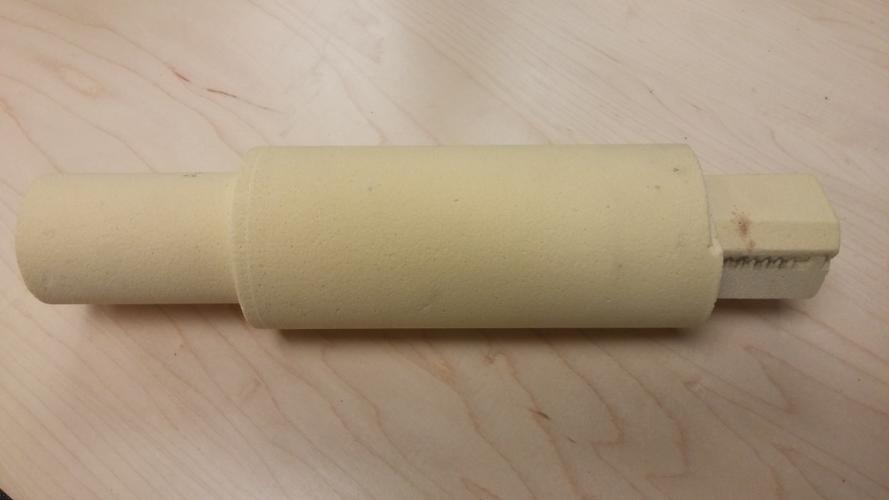
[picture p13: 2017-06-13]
Media/Shrink_fit_design/tube_liner_machining/FoamMandrel_small.jpg

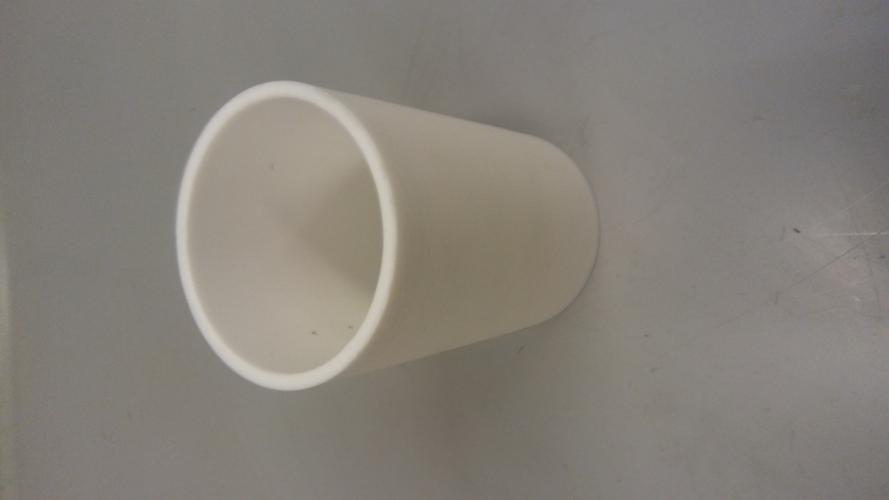
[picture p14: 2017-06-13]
Media/Shrink_fit_design/1-8_ Tube Liner Layup Pics/20170531_143853_small.jpg

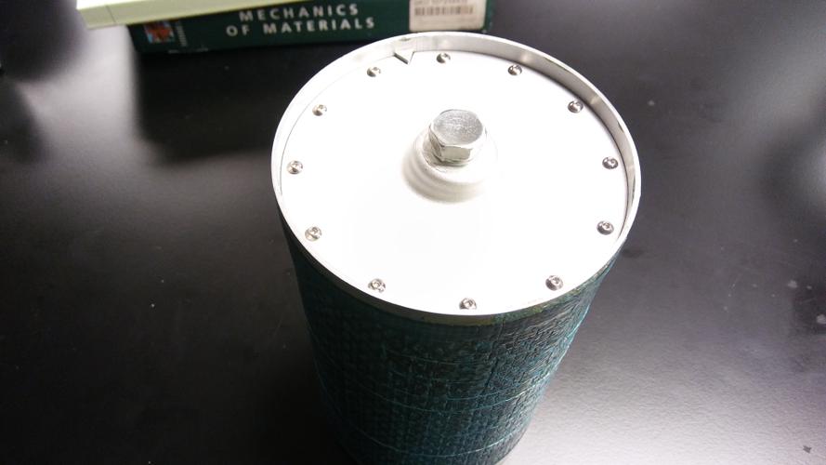
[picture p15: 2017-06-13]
Media/Shrink_fit_design/Completed Shrink Fit Design3_small.jpg

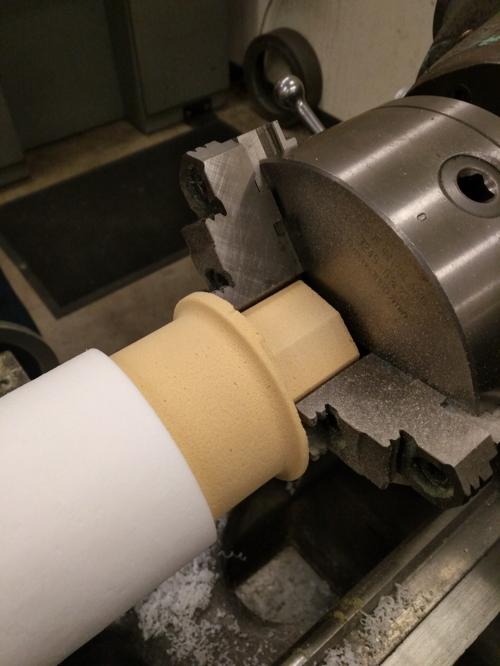
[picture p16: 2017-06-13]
Media/Shrink_fit_design/tube_liner_machining/IMG_20170512_160852_small.jpg

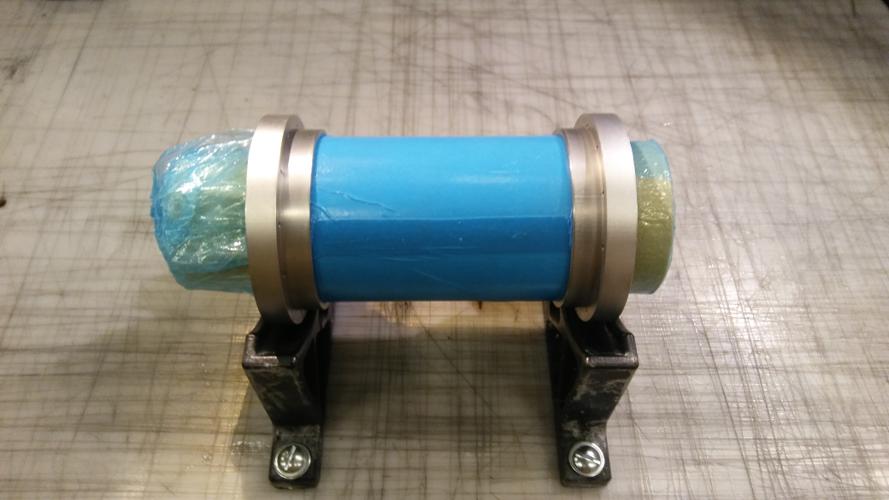
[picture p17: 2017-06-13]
Media/Shrink_fit_design/1-8_ Tube Liner Layup Pics/20170528_163248_small.jpg

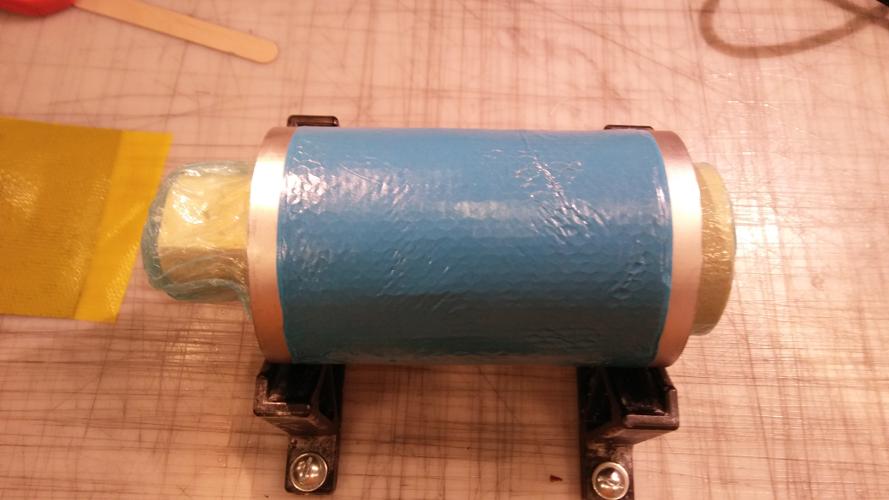
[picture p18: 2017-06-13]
Media/Shrink_fit_design/1-8_ Tube Liner Layup Pics/20170528_170735_small.jpg

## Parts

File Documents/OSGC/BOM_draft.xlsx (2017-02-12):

Budget (Page limit: As needed): The budget must reflect a clear alignment with the content and text of the proposal. Include matching support as a separate column.
Teams may submit requests for funding up to $15,000 per team. A minimum 2-to-1 match obligation is required. Matching funds include donations, discounts, team travel contributions, and faculty advisor time from non-federal sources. Funding requests may include supplies, parts, registration fees and/or lodging accommodations related to the project competition.
Items that we need to pay for: |  |  |  |  |  | Items that constitute matching
Material | Unit Cost | Quantity | Requested Amount | Links: | Notes: | Description | Acquired Via | Estimated Value | Links: | Notes:
Aerogel |  |  |  |  |  | Team Labor | Donation
6061 Aluminum | $39.63/36 cubic inches |  | $500.00 | https://commerce.cashnet.com/cashnetg/selfserve/BrowseCatalog.aspx?CNAME=1 | PSU melt (6''x6''x1'') | Nomex Honeycomb | Donation
Teflon/S-2 |  |  |  |  |  | Prepreg | Donation
Machinable Foam | $123.95/5.63 cubic feet | 20 cubic feet | $500 | http://www.sailrite.com/High-Density-Polyurethane-Foam-Firm-5-x-24-x-82 |  | Carbon Fiber | Donation
Liquid Nitrogen | approx. $4/lb (psu chem. department) | 10 liters |  | http://www.praxairdirect.com/Product2_10152_10051_114002_-1____ | requires a price quote via phone call | Capstone Sponsorship | PSAS
LOX |  | 5 liters |  | http://www.praxairdirect.com/Product2_10152_10051_67588_-1____ | requires a price quote via hpone call | Machining Labor | Donation
Aluminum Foil | $0.043/sq. ft. | 1000 sq. ft. | $43 | https://www.uline.com/Product/Detail/S-20197/Food-Service-and-Packaging/Aluminum-Foil-Roll-12-x-1000?id=S-20197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 | Just in case there is some way to creat a sealed liner
Cryogel Z (5mm) | $14/sq. ft. | 15 sq. ft. | $400 | http://www.ebay.com/itm/Aspen-Aerogels-Cryogel-Z-Aerogel-5mm-/322248010416 | For 12"x2" cylindrical modules, we need 0.523sq ft of material
Sensor and Gauges |  |  | $1000
 |  |  |  |  |  | Layup Mandrel | Machined by Arrow | $350.00 | Module18_BOM.xlsx
 |  |  |  |  |  | Dummy layup rings | Machined at PSU | $180.00 | Module18_BOM.xlsx
 |  |  |  |  |  | Orca clean | Fiberlay | $94.21 | Module18_BOM.xlsx | per gallon
 |  |  |  |  |  | Orca seal | Fiberlay | $128.88 | Module18_BOM.xlsx | per gallon
 |  |  |  |  |  | 3 Way pass quick connect hose coupler |  | $9.87 | Beta Accounting google sheet | $9.87/ea
Heat Gun, 110 to 1150F | Milwakee Heat Gun | 1 | 172.65 | https://www.zoro.com/milwaukee-heat-gun-110-to-1150f-125a-8988-20/i/G2587295/?gclsrc=aw.ds |  | Nitrile Gloves (Med and Large) | Home depot | $40.36 | http://www.homedepot.com/p/Grease-Monkey-Nitrile-Large-Disposable-Gloves-100-Count-23890/202638590 | $10.09/ea
Permabond POP Primer |  |  | $100 | http://www.permabond.com/2015/06/10/bonding-ptfe-industrial-adhesive/ | requires price quote via phone | 1/2" Kapton Tape | amazon | $27.75 | http://www.amazon.com/Mil-Kapton-Tape-Polyimide-Yds/dp/B006ZFQNT6?s=industrial | $9.25/ ea
Permabond 737 |  |  | $100 | http://www.permabond.com/2015/06/10/bonding-ptfe-industrial-adhesive/ | requires price quote via phone | Industrial Scissors |  | $27.36 | Beta Accounting google sheet | $27.36/ea
Discretionary Mat. Budget |  |  |  |  |  | Tupperware Set | Home Depot | $17.10 | http://www.homedepot.com/p/Anchor-Hocking-10-Piece-TrueSeal-Storage-Set-92093/204266910
Discretionary Machining Labor | ~$100/hr (?) |  | $1000 | https://www.chemours.com/Teflon_Industrial/en_US/products/product_by_name/teflon_ptfe/ |  | Ceramical |  | $107.24 | Beta Accounting google sheet | $26.81/ ea
PTFE Granular Molding Powder |  |  | $400 |  |  | High Temp Paste Wax |  | $19.95 | Beta Accounting google sheet | $19.95/ ea
PTFE resin wetting agent |  |  | $400 |  |  | PVA Release Film |  | $10.75 | Beta Accounting google sheet
 |  |  |  |  |  | 1 reducer adapter |  | $6.64 | Beta Accounting google sheet
 |  |  |  |  |  | Stree Elbow |  | $4.04 | Beta Accounting google sheet
 |  |  |  |  |  | Vacuum regulator |  | $109.33 | Beta Accounting google sheet
 |  |  |  |  |  | Vacuum pump oil |  | $31.90 | Beta Accounting google sheet | $6.38 /ea
 |  |  |  |  |  | Garden Hose |  | $8.10 | Beta Accounting google sheet
 |  |  |  |  |  | 320 sand paper | home depot | $6.99 | Beta Accounting google sheet
 |  |  |  |  |  | 600 grit sandpaper | Home depot | $17.91 | http://www.homedepot.com/p/3M-3-2-3-in-x-9-in-Imperial-Wetordry-800-Grit-Sandpaper-Sheets-5-Sheets-Pack-5922-18-CC/202563281 | 5.97/pack
 |  |  |  |  |  | 800 sand paper | home depot | $9.03 | Beta Accounting google sheet
 |  |  |  |  |  | 1500 sand paper | home depot | $11.94 | http://www.homedepot.com/p/3M-3-66-in-x-9-in-1500-Grit-Sandpaper-10-Sheets-Pack-5924-18-CC/205421855 | 5.97/pack
 |  |  |  |  |  | Vacuume bagging (stretchlon) | Fiberlay | $114.75 | http://www.fiberlay.com/prod-vacuum-bag-materials.php?subclass=1801001-180106160&startrow=0 | $4.59/ YD
 |  |  |  |  |  | WL5200B-P-001 release film | Fiberlay | $420.50 | http://www.fiberlay.com/prod-vacuum-bag-materials.php?subclass=1805001060-1805019&startrow=0 | $16.82 / YD
 |  |  |  |  |  | Orca Breather fabric | Fiberlay | $110.75 | http://www.fiberlay.com/prod-vacuum-bag-materials.php?subclass=1804001-1804006&startrow=0 | $4.43 / YD
 |  |  |  |  |  | Sealant Tape | Fiberlay | $18.32 | http://www.fiberlay.com/prod-vacuum-bag-materials.php?subclass=1803002-1803020&startrow=0 | $9.16 / Ea
 |  |  |  |  |  | 1" Flash Breaker Tape 72 yd Roll | ACP composites | $20.01 | https://www.acpsales.com/product.php?productid=17015 | 20.01 per roll
 |  |  |  |  |  | Assemble Screws | Tacoma Screw | $8.01 | http://www.mcmaster.com/#100-degree-flat-head-screws/=sal1lj | per 100 screws
 |  |  |  |  |  | Perforated Shrink Tape | ACP composites | $21.63 | http://www.acpsales.com/home.html | per roll
 |  |  |  |  |  | Total |  | 1933.32

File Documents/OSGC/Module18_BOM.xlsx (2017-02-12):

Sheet: Standard module BOM
Item # | Item | Part # | Qty | Source | Cost/Unit | Description | Other Sources | Link
 | Standard Module BOM
1 | Meltbond 1515-3M, 20''x16.85'' | 1515-3M | 1 | Pacific Coast Composites | Donation | Inner layer adhesive film |  | http://solutions.3m.com/wps/portal/3M/en_US/Aerospace/Aircraft/Prod_Info/Prod_Catalog/
2 | Meltbond 1515-3M, 22''x17.65'' | 1515-3M | 2 | Pacific Coast Composites | Donation | Outter layer adhesive film |  | http://solutions.3m.com/wps/portal/3M/en_US/Aerospace/Aircraft/Prod_Info/Prod_Catalog/
3 | Meltbond 1515-3M, 21''x.35'' | 1515-3M | 2 | Pacific Coast Composites | Donation | Coupling ring adhesive film |  | http://solutions.3m.com/wps/portal/3M/en_US/Aerospace/Aircraft/Prod_Info/Prod_Catalog/
4 | CYCOM 934 EPOXY PREPREG, 20''x16.85'' | BMS 8-297 3K-70-PW TY4 CL2 | 1 | Pacific Coast Composites | Donation | Inner prepreg carbon fiber ply (preferrably 5 Harness, can be plain weave) |  | http://www.cemselectorguide.com/pdf/CYCOM_934_032012.pdf
5 | CYCOM 934 EPOXY PREPREG , 22''x17.56'' | BMS 8-297 3K-70-PW TY4 CL3 | 1 | Pacific Coast Composites | Donation | Outter prepreg carbon fiber ply (preferrably 5 Harness, can be plain weave) |  | http://www.cemselectorguide.com/pdf/CYCOM_934_032012.pdf
6 | Female Mating Rings | N/A | 1 | Machine sicence | Donation | Aluminum
7 | Male Mating Rings | N/A | 1 | Machine sicence | Donation | Aluminum
8 | Honeycomb Core | N/A | 1 | Pacific Coast Composites | Donation | 1lb density,21.25''x16.94''x.25'' |  | http://www.hexcel.com/resources/honeycomb-data-sheets
9 | Assemble Screws | 93085A105 | 6 | Tacoma Screw | $8.01/100 | #4 40 100 deg countersunk screws 3/16 length | Mcmaster Carr, Fastenal | http://www.mcmaster.com/#100-degree-flat-head-screws/=sal1lj
 | Layup Tools
10 | Layup Mandrel | N/A | 1 | Machined by Arrow | $350.00 | 27''x6''OD
11 | Dummy Layup Rings | N/A | 2 | Machined in house | $180.00 | Aluminum
12 | Mandrel Screws | 93085A105 | 6 | Tacoma Screw | $8.01/100 | #4 40 100 deg countersunk screws 3/16 length | Mcmaster Carr, Fastenal | http://www.mcmaster.com/#100-degree-flat-head-screws/=sal1lj
13 | Perforated Shrink Tape | V-24A | 900" | ACP Composites | $21.63/roll | 1" Shrink Tape - Perforated/Release Coated | Pacific Coast Composites | http://www.acpsales.com/home.html
14 | Flash Tape (or kapton tape) | NA | 10" | ACP Composites | 20.01/roll | 1" Flash Breaker Tape 72 yd Roll | Pacific Coast Composites
15 | Cutout Templates | NA | 4 | Laser cut in house | NA | See description in steps 1 through 6 instruction | Tap Plastics
16 | Heat Gun | 96289 | 1 | Harbor Freight | $14.95 | 1500 Watt Dual Temperature Heat Gun | Home Depot, Mcmaster carr | http://www.harborfreight.com/1500-watt-dual-temperature-heat-gun-572-1112-96289.html
17 | Tongue Depressors | NA | 2 | Fred Meyer | 5/bag | Wood | Home Depot, Mcmaster carr
 | Powderless Nitrile Gloves |  | ~30 | Ace Hardware | ~$5/box | keep skin oil in and carcinogens out | most stores
 | release film, 20''x16.35'' |  | 1 | ??? | Donation | inner release
 | release film, 2' x 20" |  | 1 | ??? | Donation | outer release
 | vacuum bag breather, 4' x 2' |  | 1 | Boeing | Donation | breather layer
 | vacuum bag sealing tape, 16' |  | 1 | ??? | Donation | goop tape
 | vacuum bag sheet, 4' x 2' |  | 2 | Boeing | Donation | inner/outer vac bags
 | Treatment Chemicals
18 | ORCA Clean | 252202 | .25 cups | Fiberlay | $94.21/gal | Mold cleaner | Acetone or similar
19 | 3M Surface Pre-Treatment | AC-130 | 25 mL | Pacific Coast Composites | Donation | Aluminum surface treatment
20 | ORCA Seal | 252203 | .25 cups | Fiberlay | $128..88/gal | Mold sealer | Frekote 700 or similar

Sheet: Sheet1
Item | Part No. (If applicable) | Qty. | Source | Cost/Unit | Description | Other Sources | Link
Parts
Adhesive film | Old glue and New glue | 2 | Pacific Coast Composites |  | 18" x 18" and 18" x 18"
Pre-preg carbon fiber | 5 Harness Prepreg CF | 2 | Pacific Coast Composites
Aluminum mating rings | MCR and FCR | 2 |  |  | MCR and FCR
Honeycomb core | .25" Nomex core 1lb density | 1 | Pacific Coast Composites |  | 18 x 18
Fasteners |  | 20 | Tacoma Screw |  | #4 40 100 deg countersunk screws 3/16 length | Mcmaster Carr, Fastenal
Tools
Layup table | LT-001 |  | Capstone Built
Curing oven | CO-002 |  | Capstone Built
Freezer | CF-003 |  | Sung Yi |  |  | Craigslist
Tools - Consumables
Razor knife |  | 1 | Tacoma Screw | $2.50 |  | Home Depot, Mcmaster carr
Scissors |  | 1 | Tacoma Screw | $2.00 |  | Home Depot, Mcmaster carr
Layup mandrel |  | 1 | Machined by Arrow | $350.00 |  | Aluminum from EMJ
Mandrel holder stand |  | 2 | 3D Printed in house
Perforated shrink tape |  | 900" | ACP Composites |  |  | Pacific Coast Composites | http://www.acpsales.com/home.html
Flash tape |  | 10" | ACP Composites |  |  | Pacific Coast Composites
Dummy layup ring |  | 2 | Machined in house | $180.00 | Stock from Speedy Metals
Mandrel fasteners |  | 6 | Tacoma Screw | $0.50 | #4 40 100 deg countersunk screws 3/16 length | Mcmaster Carr, Fastenal
Mandrel curing stand |  | 2 | Aluminum made in house |  | Metal from Scrap
Cutout templates |  | 4 | Laser cut in house |  | Steps 1 through 6 | Tap Plastics
Shop towels |  | 2' | Tacoma Screw |  | Blue automotive towels work best | Home Depot, Mcmaster carr
Acetone |  | .25 cups | Fiberlay |  | ORCA Clean is what we use | Home Depot, Mcmaster carr
3M Alum. surface treatment |  | 25 mL | Pacific Coast Composites
Alum. treatment brush applicator |  | 1 | Tacoma Screw |  | Any standard brush works | Home Depot, Mcmaster carr
Gloves
M - Box |  | 1 | Winks |  |  | Home Depot, Mcmaster carr
XL - Box |  | 1 | Winks |  |  | Home Depot, Mcmaster carr
ORCA Hybrid Mold Release |  | .25 cups | Fiberlay
Sandpaper |  | 10 in^2 | Homedepot |  | 320 and 600 grit
Sharpie marker |  | 2 | Safeway |  | Fine Point | Home Depot, Mcmaster carr
Tongue depressors |  | 2 | Fred Meyer |  | Standard wood
Heat gun |  | 1 | Rob Melchione |  |  | Home Depot, Mcmaster carr

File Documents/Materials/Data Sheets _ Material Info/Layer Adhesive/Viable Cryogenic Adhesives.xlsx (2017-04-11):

Supplier: | Name: | Long Description: | Components: | Min/Max Temp: | Cure Temp: | Advantages | Quote: | Link:
Masterbond | EP series |  | 2 | -269/250F | Low (200F) | Probably cheapest, but would require lower prepreg cure temp
Masterbond | EP29LPSP | Master Bond Polymer System EP29LPSP is a two component, high performance, modified low temperature heat cured epoxy system specially formulated for cryogenic applications. EP29LPSP is serviceable at temperatures as low as 4K as an adhesive, sealant and protective coating, but more importantly, it is able to withstand cryogenic shocks (i.e. room temperature down to liquid helium temperatures in a 5-10 minute time period). This optically clear, low viscosity epoxy bonds well to a wide variety of substrates including metals, glass, ceramics, composites and many different plastics. The working life is long; a 100 gram mass will allow over 4-5 hours of working life. EP29LPSP has superior electrical insulation properties and a good chemical resistance profile. EP29LPSP requires gelling the mixed epoxy at room temperature, followed by alternative lower elevated temperature cure cycles (8-10 hours at 130-150°F) or (5-7 hours at 175°F) or (3-5 hours at 200°F). EP29LPSP is widely used in applications requiring cryogenic service, optical clarity and NASA low outgassing properties. | 2 | -269/??? | Low (200F) | Can withstand rapid temperature changes. bonds well to metals, composites, and plastics. Good Chemical resistance? Low outgassing. | To be requested | http://www.masterbond.com/tds/ep29lpsp
Masterbond | EP29LPSPAO | Master Bond EP29LPSPAO is a two component, thermally conductive, electrically insulative, high performance epoxy system. It is specially formulated for cryogenic applications and requires a relatively low temperature heat cure.EP29LPSPAO is serviceable at temperatures as low as 4K as an adhesive, sealant, coating and encapsulant, but more importantly, it is able to withstand cryogenic shocks (i.e. room temperature down to liquid helium temperatures in a 5-10 minute time period). This low viscosity epoxy adheres well to a wide variety of substrates including metals, glass, ceramics and many different plastics, and is ideal for potting and encapsulation. The working life is exceptionally long; a 100 gram mass will allow over 5-7 hours of working life. EP29LPSPAO has superior electrical insulation properties and a good chemical resistance profile. The optimum cure schedule for EP29LPSPAO requires gelling the mixed epoxy at room temperature, followed by alternative lower elevated temperature cure cycles (8-10 hours at 130-150°F) or (5-7 hours at 175°F) or (3-5 hours at 200°F). EP29LPSPAO is widely used in applications where thermal conductivity and cryogenic serviceability are required. The mixed system is off white in color. | 2 | -269/250F | Low (200F) | Can withstand rapid temperature changes. bonds well to metals, composites, and plastics. Good Chemical resistance? Low outgassing. | To be requested | http://www.masterbond.com/tds/ep29lpspao
Masterbond | EP 21 Series |  |  |  |  | Probably cheaper than Supreme Series
Masterbond | EP21TCHT-1 | Master Bond EP21TCHT-1 is a two component, thermally conductive, heat resistant epoxy compound formulated to cure at ambient temperatures or more rapidly at elevated temperatures. EP21TCHT-1 has a 100:60 mix ratio by weight. Most significantly, it passes NASA low outgassing tests with exceptionally sterling numbers. EP21TCHT-1 offers an array of outstanding physical properties once cured. The system is an excellent, high strength adhesive that conducts heat, yet is electrically insulative. This epoxy can withstand rigorous thermal cycling and shocks. It is highly distinctive in that it possesses high temperature resistance as well as superlative cryogenic serviceablilty. Its actual service temperature range is from 4K to +400°F. It bonds well to a wide variety of substrates, including composites, metals, ceramics, glass and many rubbers and plastics. EP21TCHT-1 resists many chemicals including water, oils, fuels and many acids and bases. Its thermal expansion coefficient is remarkably low, as indicated below. For an epoxy system, its dimensional stability is second to none. The color of Part A and Part B is off-white. EP21TCHT-1 is widely used in aerospace, electronics, electrical, semiconductor, and cryogenic applications. As a NASA qualified system, it is ideal for high vacuum type applications, particularly those where only slightly elevated temperature cures are possible. However, the best curing schedule to optimize properties is overnight at room temperature followed 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 | 2 | -269/400F | Low (Room/200F) | Can withstand high temps, chemically resistant, can bond to composites, metals, and plastics. Resistant to rigorus thermal cycling and shocks | To be requested | http://www.masterbond.com/tds/ep21tcht-1
Masterbond | Supreme Series |  | 1 | -269/400+F | Med/Higher(250~300F) | Can withstand high temps, high shear and peel strength, can bond to composites, metals, and many plastics. Resistant to severe thermal cycling.
Masterbond | Supreme 10AOHT | Master Bond Supreme 10AOHT has a remarkable combination of properties highlighted by excellent thermal conductivity, superior electrical insulation and the ability to withstand rigorous thermal cycling. This one component, non-mix system, which is not premixed and frozen, has an unlimited working life at room temperature. It cures with minimal shrinkage in 60-70 minutes at 250°F or 40-50 minutes at 300°F. It has extraordinary bond strength, particularly its tensile lap shear strength of over 3,500 psi. It bonds well to a wide variety of substrates, including metals, composites, glass, ceramics and many plastics. Supreme 10AOHT is 100% reactive and does not contain any solvents or diluents. The service temperature range is particularly striking, extending from 4K to +400°F. Supreme 10AOHT is a toughened system with superior resistance to aggressive thermal cycling and shock. It is notable for its dimensional stability and its impressive array of physical strength properties. Supreme 10AOHT has high caliber chemical resistance, particularly to water, oil, fuels and solvents. It is gray in color. Supreme 10AOHT is widely used for bonding and sealing in aerospace, electronic, electro-optic, specialty OEM and related applications, where the wonderful combination of convenient processing and handling along with the superb performance profile mentioned previously is highly desirable. | 1 | -269/400+F | Med/Higher(250~300F) | Can withstand high temps, high shear and peel strength, can bond to composites, metals, and many plastics. Resistant to aggressive thermal cycling and shock. Low outgassing | To be requested | http://www.masterbond.com/tds/supreme-10aoht
Masterbond | Supreme 10HTFL | Master Bond Supreme 10HTFL, an epoxy that features good toughness, combines convenient processing and a superior physical strength profile. From the handling perspective, Supreme 10HTFL is a true one part system. It is not premixed and frozen and has unlimited working life at room temperature. It is relatively faster curing with typical cure schedules of 20-30 minutes at 300°F or 45-60 minutes at 250°F. Post curing for 1-2 hours at 250-300°F will help to optimize the properties. It is a smooth high viscosity system that flows well. Supreme 10HTFL has an attractive array of advantageous physical strength and electrical insulation properties. Most importantly, it is a forgiving epoxy, that is to say, it is less rigid than typical high temperature resistant epoxies. This “toughness” gives Supreme 10HTFL superior resistance to impact, thermal and mechanical shock and vibration, and allows it to be used in applications with rigorous thermal cycling. The system is a good option when bonding substrates with different coefficients of thermal expansion. In this context, it should be noted that it bonds well to a wide variety of substrates including metals, glass, composites, ceramics, rubber and many plastics. An additional feature of Supreme 10HTFL is its wide temperature range of 4K to +350°F. It is 100% reactive and does not contain any solvents or diluents. It has good chemical resistance to water, oils, fuels and many cleaning agents. As mentioned before, the epoxy has excellen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 | 1 | -269/400+F | Med/Higher(250~300F) | Can withstand high temps, high shear and peel strength, can bond to composites, metals, and many plastics. Resistant to aggressive thermal cycling and shock. Good for bonding materials with different coefficients of thermal expansion. |  | http://www.masterbond.com/tds/supreme-10htfl
Masterbond | Supreme 12AOHT-LO | Master Bond Supreme 12AOHT-LO has an impressive combination of easy and straightforward processing along with an array of superb properties after curing. It is a single component system that cures at 125°C (257°F) in 60-70 minutes and 150°C (302°F) in 40-50 minutes. There is no need for it to be stored frozen. Additionally, it has unlimited working life at room temperature. Upon cross-linking, Supreme 12AOHT-LO has numerous favorable attributes highlighted by excellent thermal conductivity, superior electrical insulation and the ability to withstand rigorous thermal cycling. It bonds well to a wide variety of substrates, including metals, composites, glass, ceramics and many plastics. This epoxy has formidable bond strength, particularly in the shear mode, exceeding 3,500 psi. The service temperature range is eye-catching, extending from 4K to +500°F. Also, it truly qualifies as a NASA low outgassing system. Along with the attractive profile, this structure has superlative dimensional stability and a robust aggregation of physical strength properties. Supreme 12AOHT-LO is a toughened system with superior resistance to aggressive thermal cycling and shock. It is notable for its dimensional stability and its impressive array of physical strength properties. Supreme 12AOHT-LO has ample chemical resistance, particularly to water, oil, fuels and solvents. It is gray in color. Supreme 12AOHT-LO is a compelling choice for bonding and sealing in aerospace, electronic, electro-optic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 | 1 | -269/500+F | Med(125C) | Can withstand high temps, extremely high shear strength, can bond to composites, metals, and many plastics. Resistant to aggressive thermal cycling and shock. |  | http://www.masterbond.com/tds/supreme-12aoht-lo

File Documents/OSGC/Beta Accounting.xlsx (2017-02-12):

Item | Cost/Unit | Approximate Need | Total
3 Way pass quick connect hose coupler | $9.87/ea | 1 | $9.87
Nitrile Gloves (Med and Large) | $10.09/ea | 4 | $40.36
1/2" Kapton Tape | $9.25/ ea | 3 | $27.75
Industrial Scissors | $27.36/ea | 1 | $27.36
42 Piece Tupperware Set | $15.99 | 1 | $15.99
Ceramical | $26.81/ ea | 4 | $107.24
High Temp Paste Wax | $19.95/ ea | 1 | $19.95
PVA Release Film | $10.75 | 1 | $10.75
1 reducer adapter | $6.64 | 1 | $6.64
Stree Elbow | $4.04 | 1 | $4.04
Vacuum regulator | $109.33 | 1 | $109.33
Vacuum pump oil | $6.38 /ea | 5 | $31.90
Garden Hose | $8.10 | 1 | $8.10
320 sand paper | $6.99 | 1 | $6.99
800 sand paper | $9.03 | 1 | $9.03
1500 sand paper | $11.94 | 1 | $11.94
 | Total: |  | $447.24

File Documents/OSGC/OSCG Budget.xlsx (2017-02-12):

Item | Description | Vendor | Amount | Matching
6061 Aluminum | Material for rings and mold | Metal Supermarket | $800 |  | https://www.metalsupermarkets.com/metals/aluminum/aluminum-6061-round-bar/
Machinable Foam | Material for composite mold | Sailrite | $200
Liquid Nitrogen | 40 gallons of liquid nitrogen for fill and drain cryogenic testing | PSU Chemistry Stockroom | $140
Liquid Nitrogen Handling | Protection equipment | PSU Chemistry Stockroom | $100
Liquid Oxygen | 40 gallons of liquid oxygen for cryogenic test | Airgas | $200
Aluminum Foil | 1000 sq ft. insulation material | Uline | $43
Cryogel Z | 30 sq ft. insulation material | Aspen | $900
PTFE | Molding powder, and resin wetting agent for tank liner | Chemours | $1800
Plain Weave Carbon Fiber Prepreg | Composite material | Pacific Coast Composites |  | $3500
Nomex Honeycomb | Core material for composite | Pacific Coast Composites |  | $2000
Meltbond | 3M composite structural adhesive | Pacific Coast Composites |  | $2500 | PCC $3600
Aluminum mating rings | Material and machining for manufacturing mating rings (12 rings) | Machine Sciences |  | $3600
Layup Mandrel | Mold for composite layup | Arrow |  | $350
Aluminum dummy layup rings | Mold assembly part | PSU Melt |  | $180
Mechanical Components | Seals, gaskets, plumbing fittings | Various Vendors | $1000
Sensors and Gauges | Sensors and gauges for cryogenic testing | HBM | $1500
Discretionary Machining Labor |  |  | $2000
Sandpaper | Sandpaper of varying grit | Home depot |  | $50
Vacuum Bagging Material | Vacuum bags, Breather fabric, sealant tape, and release film | Fiberlay |  | $770
Vacuum Pump Equipment | Pump regulator, pump oil, reducer adapter, hose |  |  | $180
Orca Seal | Solvent for mold surface treatment | Fiberlay |  | $130
Orca Clean | Solvent for mold surface treatment | Fiberlay |  | $100
Compression molding material | Shrink tape, kapton tape, industrial scissors, ceramical | Various Vendors |  | $230
Heat gun | Heat gun for composite layup | Milwaukee | $180
Dr. Jun Jiao's Consulting Time | 1 hour per week, Jan - Jun (20 weeks) at $100/hr |  |  | $2000
Future Material Donations | Future material donations from Boeing, Pacific Coast Composites |  |  | $6000
Future Services Donations | Material and machining time from Machine Sciences Corporation |  |  | $3000
Total |  |  | $8863 | $24590

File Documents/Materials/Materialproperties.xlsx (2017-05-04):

Material Properties
 | Material | PTFE (General) |  | Source
 |  | CTE of Teflon PTFE (+25 to -190C) | 86e-6 +/- 3e-6 m/m-C | (1956 Kirby text)
 |  | CTE (linear) | 112-135 e-6m/m-K | http://www.engineeringtoolbox.com/linear-expansion-coefficients-d_95.html
 |  | Elasticity
 |  | Yield Strength
 |  | Shear Strength
 |  | Aluminum (6061 T6)
 |  | CTE, linear | 13.1*10^-6 in/in-F | matweb (http://www.matweb.com/search/datasheet_print.aspx?matguid=1b8c06d0ca7c456694c7777d9e10be5b) | http://www.performancecomposites.com/about-composites-technical-info/124-designing-with-carbon-fiber.html
 |  | Specific Heat Capacity | 0.214 BTU/lb-F, 0.896 J/g-C | matweb (http://www.matweb.com/search/datasheet_print.aspx?matguid=1b8c06d0ca7c456694c7777d9e10be5b)
 |  | Thermal Conductivity | 1160 BTU-in/hr-ft^2-F, 167 W/m-K | matweb (http://www.matweb.com/search/datasheet_print.aspx?matguid=1b8c06d0ca7c456694c7777d9e10be5b)
 |  | Ultimate Tensile Strength | 45000 psi, 60000 psi (at -321 F) | matweb (http://www.matweb.com/search/datasheet_print.aspx?matguid=1b8c06d0ca7c456694c7777d9e10be5b)
 |  | Yield Strength | 40000 psi, 47000 psi (at -321 F) | matweb (http://www.matweb.com/search/datasheet_print.aspx?matguid=1b8c06d0ca7c456694c7777d9e10be5b)
 |  | Elastic Modulus | 10000 ksi | matweb (http://www.matweb.com/search/datasheet_print.aspx?matguid=1b8c06d0ca7c456694c7777d9e10be5b)
 |  | Poissons Ratio | 0.33 | matweb (http://www.matweb.com/search/datasheet_print.aspx?matguid=1b8c06d0ca7c456694c7777d9e10be5b)
 |  | Shear Strength | 30000 psi | matweb (http://www.matweb.com/search/datasheet_print.aspx?matguid=1b8c06d0ca7c456694c7777d9e10be5b)
 |  | Carbon Fiber (Toray FL6673G-37KT)
 |  | CTE | -0.4 to -1.0*10^-6/K | http://www.toraycfa.com/product.html | http://www.matweb.com/search/MaterialGroupSearch.aspx
 |  | Tensile Strength | 128 ksi, 883 MPa | Toray 3900 data sheet
 |  | Modulus of Elasticity | 9.9 msi, 68 GPa | Toray 3900 data sheet
 |  | Compression Strength (after impact) | 47.5 ksi, 328 MPa | Toray 3900 data sheet
 |  | Compression Strength | 206 ksi, 1420 MPa | Toray 3900 data sheet
 |  | Fiber Areal Weight | 196 g/sq m | Toray 3900 data sheet
 |  | Carbon Fiber Resin Data | Resin content 40 weight % | Toray 3900 data sheet
 |  | Tensile Strength | 13.9 ksi, 95.8 MPa | Toray 3900 data sheet
 |  | Elastic Modulus | 0.505 msi, 3.48 GPa | Toray 3900 data sheet
 |  | Strain (%) | 4.7 | Toray 3900 data sheet
 |  | Compression Strength | 22.5 ksi, 155 MPa | Toray 3900 data sheet
 |  | Compression Modulus | 0.459 msi, 3.16 GPa | Toray 3900 data sheet
 |  | Strain (%) | 11.6 | Toray 3900 data sheet
 |  | Flexure Strength | 21.1 ksi, 146 MPa | Toray 3900 data sheet
 |  | Flexure Modulus | 0.423 msi, 2.92 GPa | Toray 3900 data sheet
 |  | Strain (%) | 7.9 | Toray 3900 data sheet
 |  | KIC | 1.54 ksi*in^.5, 1.69 Mpa*m^.5 | Toray 3900 data sheet
 |  | Nomex Honeycomb (AHN 4120 1/4-3.0)
 |  | CTE | 19.4e-6 in/in-F | HexWeb Honeycomb Attributes and Properties
 |  | Compressive Strength (bare) | 160 psi (min) | http://www.ahtinc.com/products/AHN4120.pdf
 |  | Compressive Strength (stabilized) | 225 psi (min) | http://www.ahtinc.com/products/AHN4120.pdf
 |  | Shear Strength (L Direction) | 127 psi (min) | http://www.ahtinc.com/products/AHN4120.pdf
 |  | Shear Modulus (L direction) | 4.5 ksi | http://www.ahtinc.com/products/AHN4120.pdf
 |  | Shear Strength (W Direction) | 64 psi (min) | http://www.ahtinc.com/products/AHN4120.pdf
 |  | Shear Modulus (W direction) | 2.5 ksi | http://www.ahtinc.com/products/AHN4120.pdf
 |  | Metlbond Structural Adhesive
 |  | Shear Strength (149 C) | 19.3 MPa | Structural Adhesives: Directory and Databook, RJ Hussey, Josephine Wilson pg 177
 |  | Shear Strength (RT) | 29 MPa | Structural Adhesives: Directory and Databook, RJ Hussey, Josephine Wilson pg 177
 |  | Peel (Bell) | 1.2 N/mm | Structural Adhesives: Directory and Databook, RJ Hussey, Josephine Wilson pg 177
 |  | Service Temp | -54 to 149 C | Structural Adhesives: Directory and Databook, RJ Hussey, Josephine Wilson pg 178

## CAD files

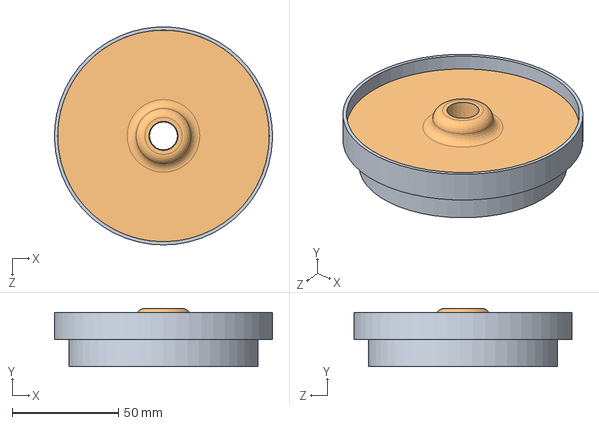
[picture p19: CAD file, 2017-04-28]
CAD/current/Simplified Shrink Fit Parts for Testing/Simplified Parts Assembly.SLDASM
102.6 x 27.4 x 102.5 mm
Main Ring Simplified
End Cap Simplified

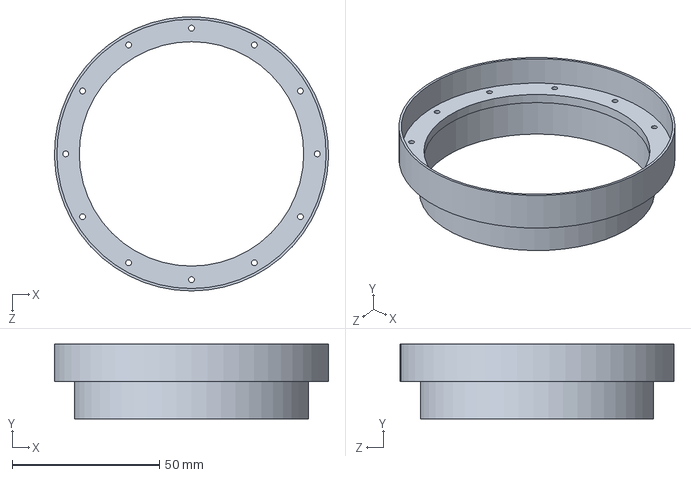
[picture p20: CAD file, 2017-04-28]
CAD/current/Flat End Cap Model (0.031-in Sheet Liner)/0202-A; Main Ring.SLDPRT
93.0 x 25.4 x 93.0 mm

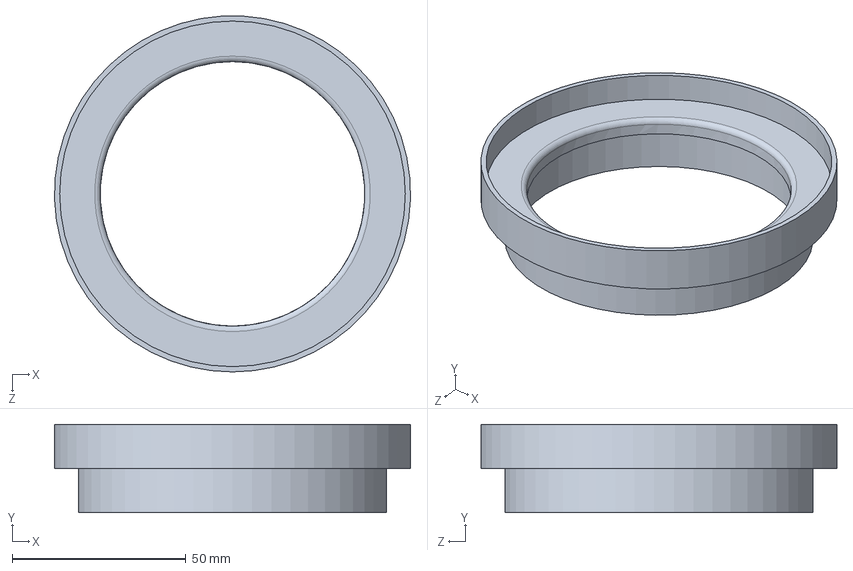
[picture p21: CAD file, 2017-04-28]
CAD/current/Simplified Shrink Fit Parts for Testing/Main Ring Simplified.SLDPRT
102.6 x 25.4 x 102.5 mm

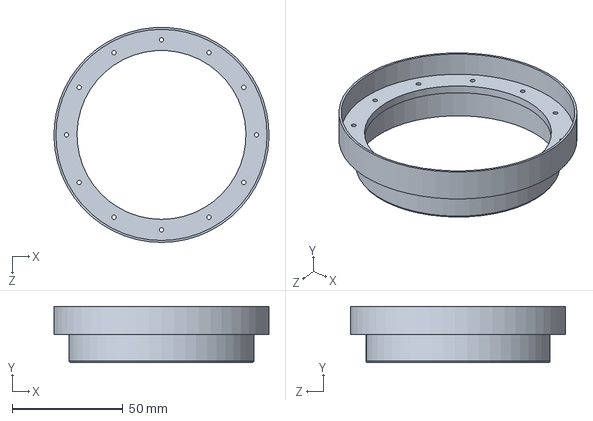
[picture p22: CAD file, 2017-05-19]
CAD/current/Flat End Cap Model (0.0625-in Tube Liner)/0201-B; Main Ring.SLDPRT
97.0 x 25.4 x 96.9 mm

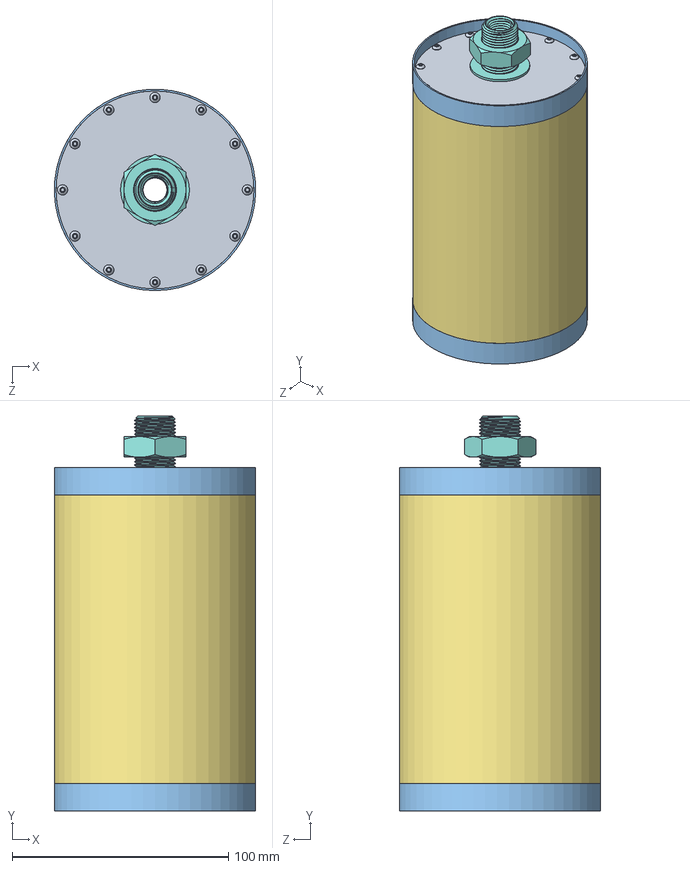
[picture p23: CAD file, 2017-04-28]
CAD/current/Flat End Cap Model (0.031-in Sheet Liner)/Cryo Tank.SLDASM
93.0 x 182.6 x 93.0 mm
0302-A; End Cap x 2
Liner
0202-A; Main Ring x 2
0602-A; Ring Seal x 2
CF Inner Layer
Honeycomb Core
CF Outer Layer
50785K273_MED-PRESSURE BRASS THREADED PIPE FITTING
92949A325_18-8 SS BUTTON-HEAD SOCKET CAP SCREW x 24

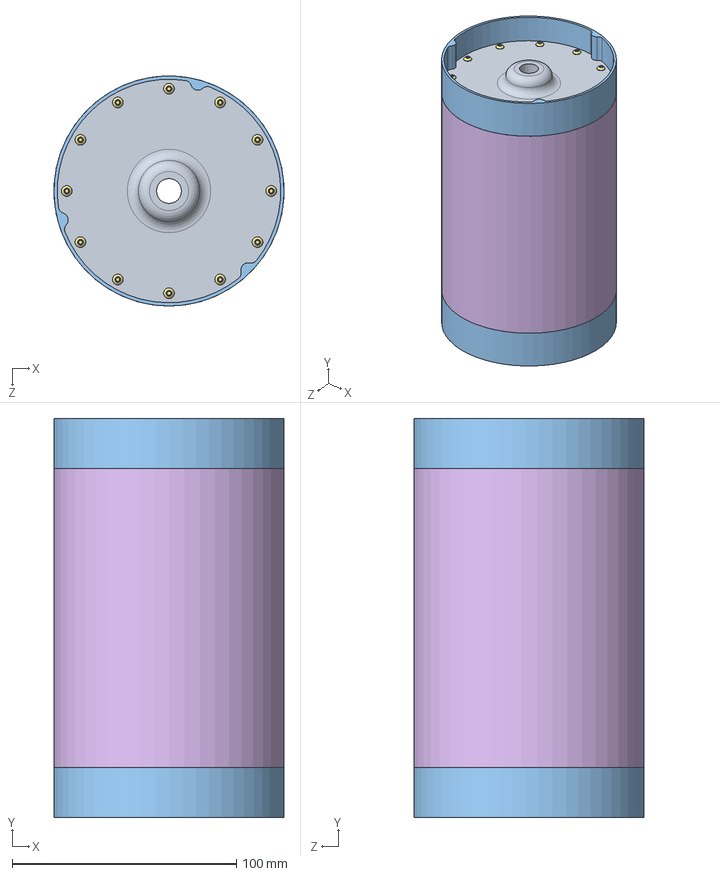
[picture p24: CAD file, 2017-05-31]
Design/CAD/current/Shrink Fit Model V2 (0.125-in Tube Liner)/Cryo Tank.SLDASM
102.5 x 177.8 x 102.6 mm
0301-C; End Cap x 2
Liner
0201-C; Main Ring x 2
CF Inner Layer
Honeycomb Core
CF Outer Layer
92949A325_18-8 SS BUTTON-HEAD SOCKET CAP SCREW x 24
Inner Honeycomb Layer

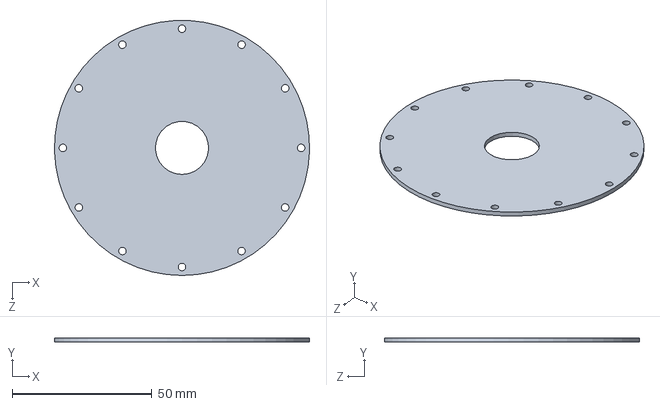
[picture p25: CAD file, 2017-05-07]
CAD/current/Flat End Cap Model (0.031-in Sheet Liner)/0302-A; End Cap.SLDPRT
91.4 x 1.59 x 91.4 mm

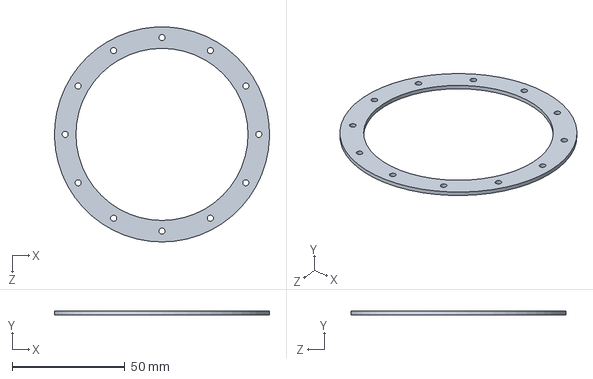
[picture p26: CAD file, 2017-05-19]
CAD/current/Flat End Cap Model (0.0625-in Tube Liner)/0601-B; Ring Seal.SLDPRT
95.2 x 1.59 x 95.2 mm

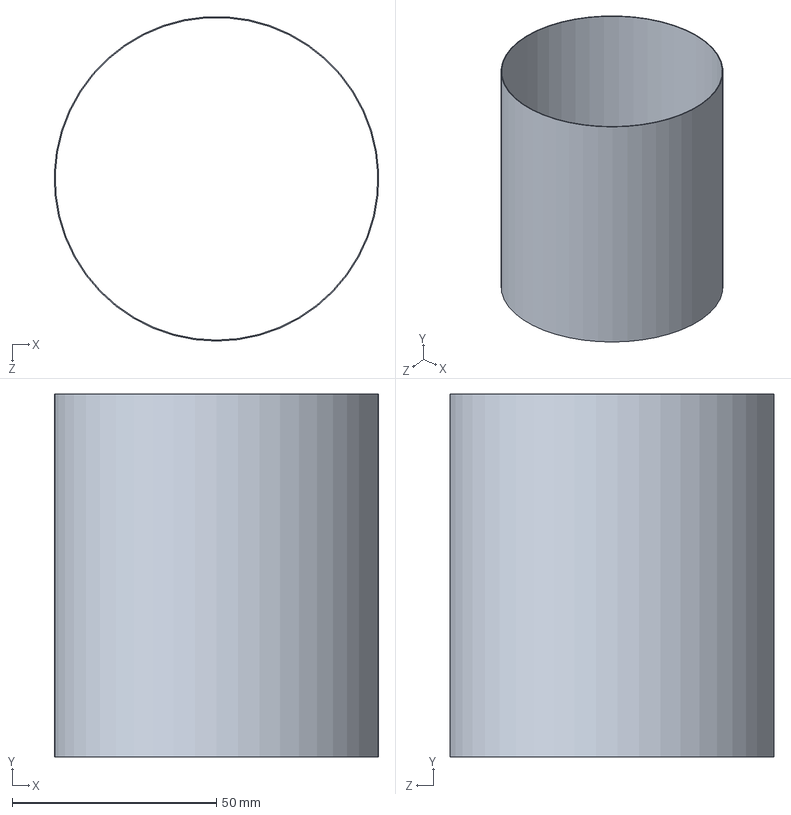
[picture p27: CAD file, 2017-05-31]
Design/CAD/current/Shrink Fit Model V2 (0.125-in Tube Liner)/CF Inner Layer.SLDPRT
79.5 x 88.9 x 79.4 mm

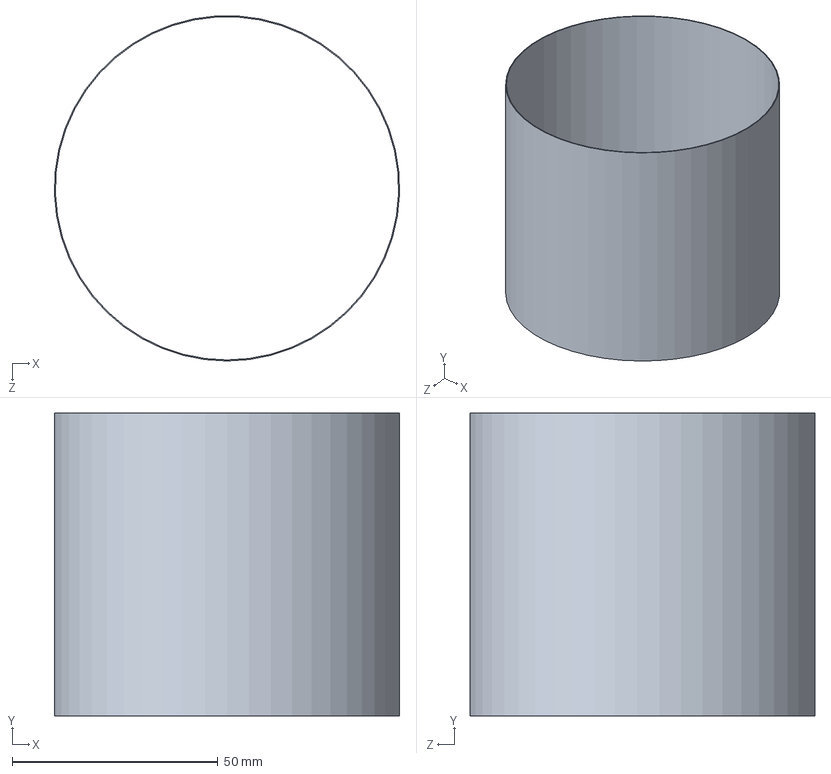
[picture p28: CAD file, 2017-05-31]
Design/CAD/current/Shrink Fit Model V2 (0.125-in Tube Liner)/CF Outer Layer.SLDPRT
83.8 x 73.6 x 83.8 mm

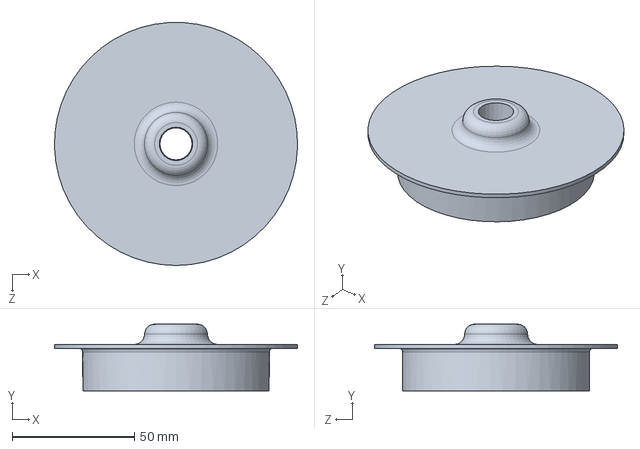
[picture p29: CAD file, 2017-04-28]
CAD/current/Simplified Shrink Fit Parts for Testing/End Cap Simplified.SLDPRT
99.5 x 27.4 x 99.5 mm

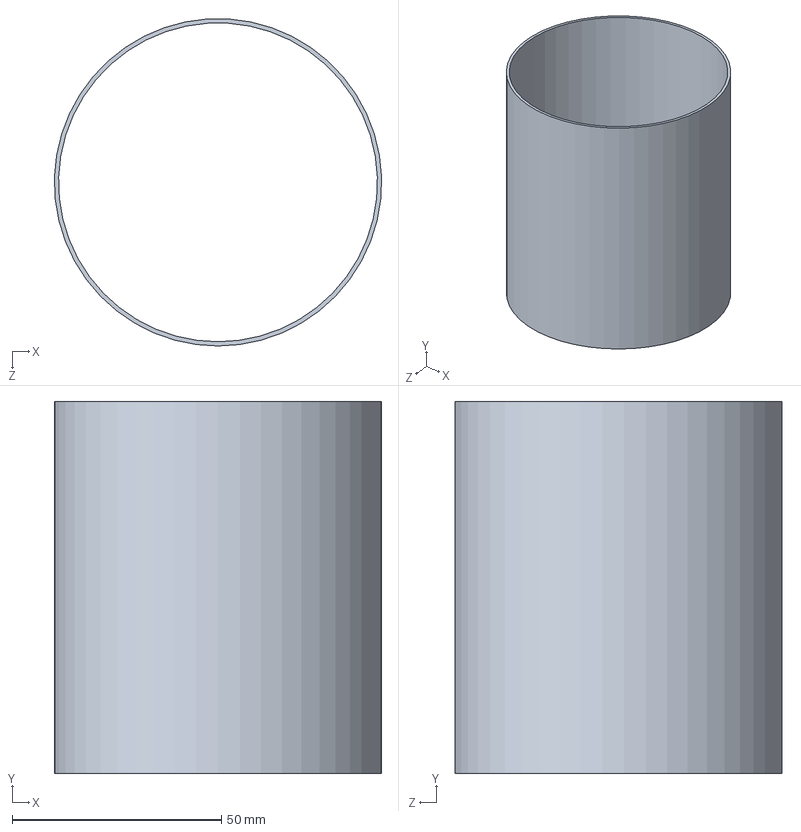
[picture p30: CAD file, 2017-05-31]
Design/CAD/current/Shrink Fit Model V2 (0.125-in Tube Liner)/Liner.SLDPRT
78.2 x 88.9 x 78.1 mm

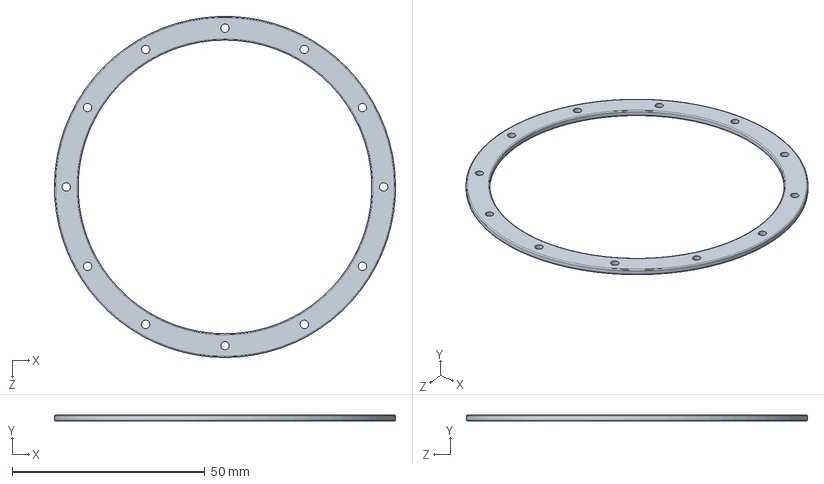
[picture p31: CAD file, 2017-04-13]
CAD/current/Second_model_20170414/Ring Seal.SLDPRT
88.5 x 1.59 x 88.5 mm

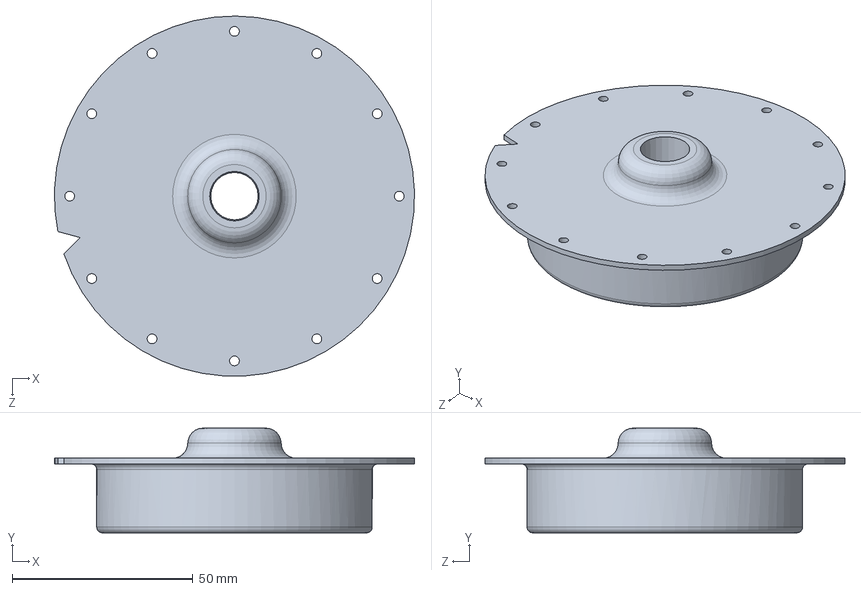
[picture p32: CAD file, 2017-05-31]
Design/CAD/current/Shrink Fit Model V2 (0.125-in Tube Liner)/0301-C; End Cap.SLDPRT
99.5 x 29.0 x 99.5 mm

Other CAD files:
Design/CAD/current/Shrink Fit Model V2 (0.125-in Tube Liner)/0201-C; Main Ring.SLDPRT
CAD/current/Flat End Cap Model (0.031-in Sheet Liner)/CF Inner Layer.SLDPRT
CAD/current/Flat End Cap Model (0.031-in Sheet Liner)/Liner.SLDPRT
CAD/current/Flat End Cap Model (0.031-in Sheet Liner)/CF Outer Layer.SLDPRT
CAD/Archive/Flat End Cap Model (0.031-in Sheet Liner)/old screws/90273A015_ZINC-PLATED STL FLAT HEAD PHIL MACHINE SCREW.SLDPRT
CAD/Archive/Flat End Cap Model (0.0625-in Tube Liner)/old screws/90273A015_ZINC-PLATED STL FLAT HEAD PHIL MACHINE SCREW.SLDPRT
CAD/Archive/Flat End Cap Model (0.125-in Tube Liner)/old screws/90273A015_ZINC-PLATED STL FLAT HEAD PHIL MACHINE SCREW.SLDPRT
CAD/current/Flat End Cap Model (0.031-in Sheet Liner)/0202-A; Main Ring.SLDDRW
CAD/current/Flat End Cap Model (0.031-in Sheet Liner)/0202-A; Main Ring.STL
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

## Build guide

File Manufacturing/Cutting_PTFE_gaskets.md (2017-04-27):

# PTFE gasket Cutting

To determine if we can cut PTFE gaskets on a laser cutter a few things needed to be done.

*  Check for safety
*  Get permission from Mike to cut a material not listed in the acceptable materials list for the laser cutter
*  Determine if the material will cut well

## Safety 
The MSDS shows that it has no flash point. It also states to ensure good ventilation if there is  the possibility of fumes. When laser cutting there will be fumes. The Laser cutter in 480 has ample ventilation.
## Get Permission
When I talked to Mike at first he said no, I then explained what I wanted to do. Because the material that we will be cutting is very thin he agreed to let us cut the gaskets with the laser.
##  Determining Power and speed of the laser
To ensure a good cut is made I made a few test cuts on the PTFE gasket material. The geometry of these test cuts were circles the size of the clearance holes. I first started with a medium power with a high speed. This cut failed to cut all the way through the material with one pass. I then slowed down the speed of the laser head to 10% and the cut was smooth with no visible discolorations of the material. The holes were cut in the far corner of the material to reduce any wasted material. The holes were also visibly perfect.

### Notes for cutting PTFE gasket
Follow Melts guidelines on their website for using the laser cutter. When it come time to select what material you are cutting there is not PTFE setting. There is a tab for custom settings. currently I recommend 50% power and 10% speed.

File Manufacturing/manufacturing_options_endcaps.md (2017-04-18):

What are the manufacturing options for the tank end cap?

***Machining with CNC mill***

**Manufacturing videos**

-   3 axis milling for the outer part of the dome: [*https://www.youtube.com/watch?v=uh9xZiqeF04*](https://www.youtube.com/watch?v=uh9xZiqeF04)

-   5 axis milling for the inner part of the dome: [*https://www.youtube.com/watch?v=NUoIzkCSpag*](https://www.youtube.com/watch?v=NUoIzkCSpag)

**Pros**

-   No machine/labor cost to machine the part in-house (if the part only requires a 3-axis CNC mill).

-   Lower lead time.

-   Reproducible for future PSAS teams.

**Cons**

-   More material relative to other manufacturing processes.

-   The end-product might be thicker, heavier.

**Questions**

-   How do we fix a round part so we can machine both sides of the dome?

**Potential Vendors**

-   [*http://www.ppmfg.com/*](http://www.ppmfg.com/)

-   PSU melt

-   PSU physics machine shop

-   [*https://www.protolabs.com/*](https://www.protolabs.com/)

-   [*http://usherprecision.com/*](http://usherprecision.com/)

***Hydroforming***

**Manufacturing videos**

-   [*https://www.youtube.com/watch?v=n-ht\_5Ysurc*](https://www.youtube.com/watch?v=n-ht_5Ysurc)

**Pros**

-   Amalco will give parts for free if you want a small number of units (you must pay for set up)

-   Less expensive than other metal forming methods, such as deep drawing when producing small quantities.

-   Dome cross section is thinner.

-   Can scale up to larger diameters.

**Cons**

-   Potentially long lead time.

-   Cost for set-up fee.

**Questions**

-   Do they have standard sizes that fit our needs?

-   Can we machine threaded holes in the part?

-   How does this constrain the geometry of the part?

**Potential vendors**

[*http://usherprecision.com/*](http://usherprecision.com/)

[*http://www.amalco.com/hydroforming-oregon.html*](http://www.amalco.com/hydroforming-oregon.html)

<span id="_gjdgxs" class="anchor"></span>

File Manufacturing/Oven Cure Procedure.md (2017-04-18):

According to Prepreg data sheet: Ramp temperature 50℉ every 10 min to reach 350℉

According to Joe: Ramp temperature 25℉ every 10 min to reach 350℉

Hold at 350℉ for 2 hours

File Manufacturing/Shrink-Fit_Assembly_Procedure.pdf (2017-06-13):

1

## PSAS Composite Fuel Tank: Shrink-Fit Assembly

### Purpose and Scope:

The intent of this procedure is to provide direction for the assembly of a proof-of-concept shrink-fit fuel tank prototype module. The tank fabrication process can be found in a separate document.

### Tools and Equipment:

The following materials and equipment should be collected and on hand at the beginning of the lay up procedure:
- Complete fabricated shrink-fit tank module
- Shrink-fit end caps (qty 2)
- Liquid nitrogen (LN2)
- Mallet
- Insulated gloves (for handling cryogenic material and heated module)
- Foam cooler (for holding LN2 during procedure)
- Tongs

### Facility Equipment:

- Exhaust fans or hoods
- Autoclave (for heating module)

### Safety:

- Insulated gloves should be worn whenever handling materials in or around LN2 or while moving module into or out of the autoclave.
- Safety glasses should be worn at all times.

### Initial Tips/Suggestions:

- The materials only remain at working temperatures for about a minute, so work quickly.
- Have at least two people to perform the procedure (one pulling the hot module and the other pulling the chilled end caps).

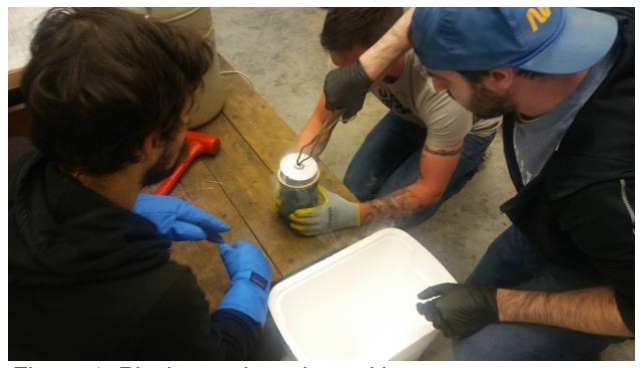
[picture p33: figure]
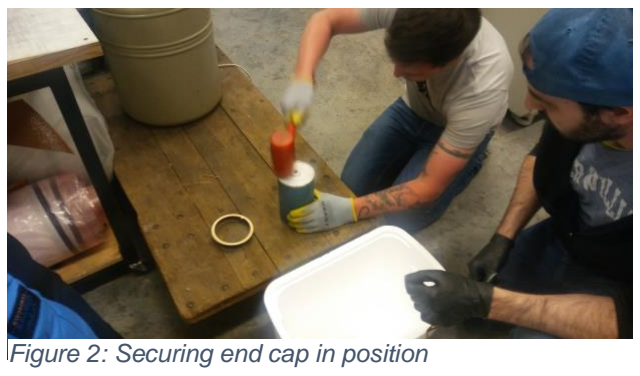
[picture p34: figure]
Figure 2: Securing end cap in position
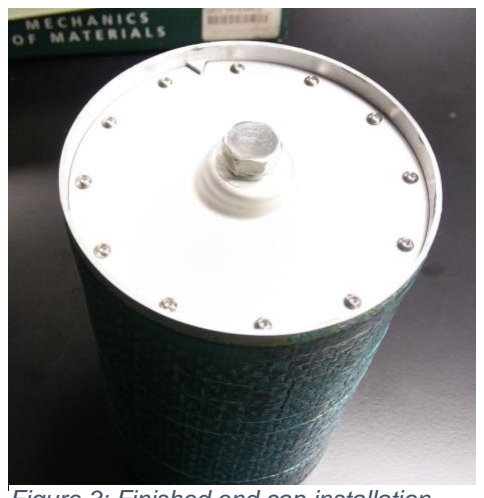
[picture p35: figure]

2

Figure 1: Placing end cap in position

### General Requirements:

This assembly procedure only reflects the steps taken in the assembly of modules for testing. It does not address steps that should be taken to minimize stresses the finished tank is exposed to in the assembly process.
Materials:
1. Turn the autoclave on and set the temperature to 250F
2. Place the module in the autoclave
3. Fill the foam cooler with enough LN2 to fully submerge end caps
4. Place end caps in cooler and replace lid

### Assembly Process:

1. Wait for the materials to come to temperature (initially this will occur when the autoclave
reaches operating temperatures)
2. Remove module from autoclave and place on workbench
3. Use tongs to remove one end cap from LN2
4. Place end cap on module, aligning keyways with the guides
5. Use mallet to insert end cap completely (check closely to be sure that the end cap is
completely seated against the mating rings)
6. Replace module in the autoclave
7. Allow enough time to bring the
module back up to temperature
(~15 minutes should be plenty of time for the smaller test modules)
8. Repeat steps 2 through 5 for the other end cap
9. Insert and tighten fasteners to hold end cap in place

Figure 3: Finished end cap installation

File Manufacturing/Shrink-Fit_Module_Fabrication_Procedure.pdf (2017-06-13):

## PSAS Composite Fuel Tank: Fabrication Procedure

### Purpose and Scope:

The intent of this procedure is to provide direction for the fabrication of a proof-of-concept shrink-fit fuel tank prototype module. The tank assembly process can be found in a separate document.

### Tools and Equipment:

The following materials and equipment should be collected and on hand at the beginning of the lay up procedure:
- Machinable foam mandrel (3” OD)
- Aluminum Mating Rings¹
(qty 2)
- Aluminum End Caps¹
(qty 2)
- Templates for inner carbon fiber, Nomex, and Metlbond adhesive layers (qty 3)
- Templates for outer carbon fiber, Nomex, and Metlbond adhesive layers (qty 3)
- Template for inner lapping portion of the mating rings adhesive layers
- Nomex honeycomb material(¼” and ⅛” thick)
- Carbon fiber
- METLBOND adhesive
- Goop tape
- Shrink tape
- Kapton tape
- Release film
- Acetone compound for cleaning
- Sandpaper (3 different grits 320, 800, and 1500)
- Vacuum bag material and breather cloth
- PTFE tube machined to ⅛”

### Facility Equipment:

- Exhaust fans or hoods
- Freezer (for storage of materials)
- Oven (for curing process)
- Vacuum pump
- Heat gun (preferably with variable temperature control)
- Small plastic tubs or paper cups for water (for sanding)
- Circular razor blade

1 Ordered from www.protolabs.com

- Workstation equipped with risers on which you can perform the layup procedure

### Safety:

- Gloves (nitrile or latex) should be worn at all times to avoid contaminating working materials. Some materials are hazardous upon contact.
- When using possibly hazardous materials (cleaning agents, etc) have exhaust fans in place and operating or work under an exhaust hood.

### Initial Tips/Suggestions²

:
- Staying clean and organized is very important.
- A heat gun is critical for dealing with the adhesive film (METLBOND). However, be careful to keep it on the lowest setting as the adhesive becomes difficult to handle as it warms up.
- Adhesive film (METLBOND) can be difficult to from the backing (orange side), especially while wearing gloves. You can use a tongue depressor or razor blade against the edge after adhering it in place. Remove the orange side first, leaving the removal of the white side until you have positioned and adhered the layer.
- Take care when placing the carbon fiber as the adhesion with the METLBOND is strong and nearly instant.
- When cutting the carbon fiber sheets, take care to stay in line with the fiber as this will provide a stronger final structure.
- When creating the templates, cut them long enough to allow for some overlapping (~¼”) of the adhesive and carbon fiber layers.

### General Requirements:

This preparation procedure only reflects the steps taken in the creation of modules for testing. It does not address the steps that should be taken to prepare the aluminum parts for long term exposure to the carbon fiber and adhesive layers. For information regarding flight-ready fabrication of these parts refer to the aluminum mating rings procedure followed by the 2014 PSAS LV3.0 airframe team²

Materials:
1. Use the templates to cut all of the required carbon fiber, Nomex, and adhesive layers before beginning any work (place in freezer until needed to preserve adhesive properties).
2. It is critical to ensure that all work surfaces are clean. This includes all workbench surfaces and the surrounding floor space.
3. Arrange multiple workstations, each for a specific task to help expedite workflow.
4. Clean all the metal tools and part surfaces using acetone. All cleaned surfaces should leave no visible residue on a towel when wiped clean.

2 Some suggestions listed based on process developed by 2014 PSAS LV3.0 airframe team. <https://github.com/psas/lv3.0-airframe/blob/master/doc/mfg/LayupInstructions_2014.pdf>

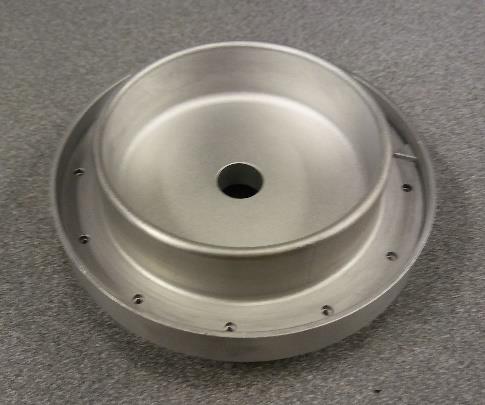
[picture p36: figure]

Figure 1: Checking end cap fit inside mating ring

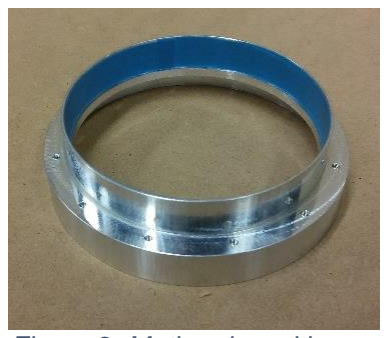
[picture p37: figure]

Figure 2: Mating ring with Metlbond adhesive applied

5. Carbon fiber: Cut one layer CF using “outer layer” template, cut roughly 2 fibers oversized. Cut one layer CF using “inner layer” template, same oversizing objective.
6. Nomex: Cut one layer from the ⅛” thick Nomex using “inner layer” template. Cut one layer from the ¼” thick Nomex using the “outer layer” template.
1. METLBOND: Cut two layers using “outer layer” template, three layers using “inner layer” template. Cut 2 strips using “ring template”

Aluminum Rings and End Caps:
1. Use the 320 grit sandpaper to sand the outer edge
of the end cap until it fits easily into position in the mating ring (check this with the end cap upside down to avoid getting the shrink-fit portions of the design stuck together).
2. Sand the interior and exterior surfaces of the lapping section of the mating rings progressing

from the 320 grit to the 800 grit and then to the
1500 grit sandpaper removing the tooling marks
from machining.
3. Using the 1500 grit paper only, sand the interior shrink-fit surface of the mating rings (this is a precise fit so be careful to not remove much material, the goal is to smooth the surface in order to negate the chance of a leak path developing in the seal)
4. Repeat step 3 on the exterior of the shrink-fit portion of the end caps.
5. Clean the mating rings and end caps using acetone and paper towels.

Mandrel:
1. Wrap the mandrel with a single layer of the release film using the Kapton tape to secure in place. Refer to the liner machining procedure for instructions on mandrel creation and preparation.

### Fabrication Process:

Mating Rings:
1. Remove the orange backing from the METLBOND and adhere the adhesive to the inside of the lapping portion of the mating rings. (In general, the heat generated by pressing and rubbing the adhesive should be enough to hold it in place. If you use the heat gun, be careful as this can cause it to adhere very strongly to the white backing.)
2. Remove the white backing from the METLBOND.

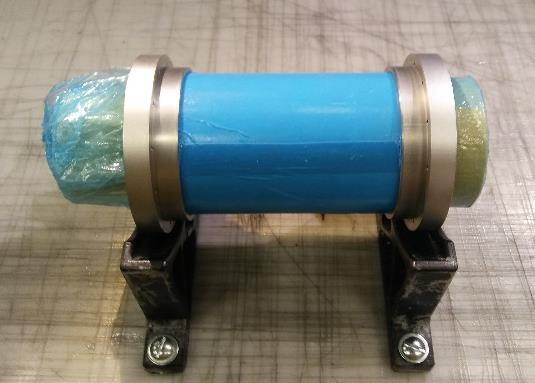
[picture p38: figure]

Figure 3: Mating rings, PTFE, assembled and mounted on mandrel with Metlbond applied

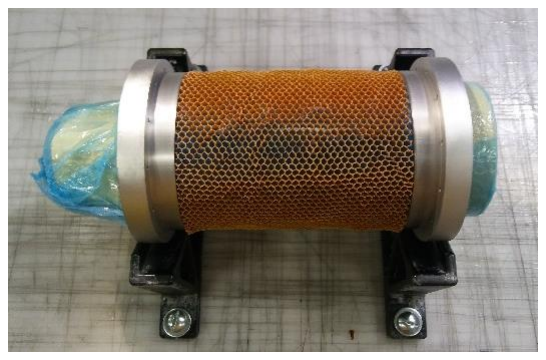
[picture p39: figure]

Figure 4: 1/8" Nomex layer

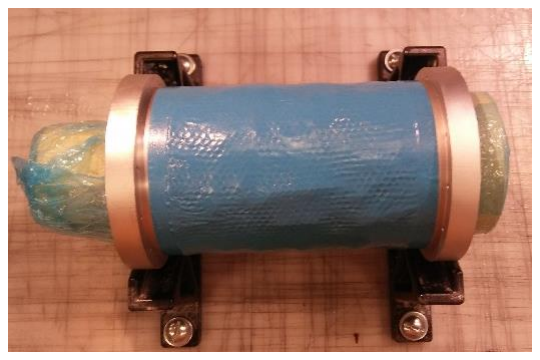
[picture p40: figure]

Figure 5: Carbon fiber and Metlbond layers applied

PTFE Liner Placement:
1. Slide the liner into position on one of the mating rings (use a tongue depressor or another similar tool if needed to keep the adhesive in place as you mount the liner in position).
2. Slide this arrangement onto the mandrel.
3. Using similar methods to the first step, mount

the second mating ring.

Lay Up Procedure:
1. Pull the working layers from the freezer, and double-check that all layers are accounted for before beginning.
a. 2 Layers of carbon fiber
b. 2 Nomex honeycomb core layers (⅛” for inner layer, ¼” for outer layer)
c. 5 layers METLBOND adhesive film (2 outer layers and 3 inner layers)

Be careful in the application of these layers to apply them as straight and evenly as possible. Best practice is one person holding the layer straight and pressing it into place while a second holds the mandrel firmly and rolls it slowly. Place the seams so they are not all aligned in the same location on the layup.

2. Peel the orange backing off of the Metlbond and adhere to the exposed surface of the PTFE using the heat of your hand to help it remain in place. Stop with about ~1” gap to remove white backing before lapping adhesive layer.
3. Remove the white backing pressing firmly on

any areas that seem to be lifting. Use the
heat gun briefly if necessary.
4. Using the heat gun on a lower setting (~350F) warm the adhesive while carefully pressing the ⅛” Nomex layer into place. It is
easiest to wrap around and adhere the seam
first, then compressing in place around the
remainder of the module.
5. Repeat steps 2 & 3 on the exterior of the Nomex layer.
6. Peel one side of yellow backing from the inner carbon fiber layer and carefully adhere in place.
7. Remove the yellow backing from the carbon fiber.

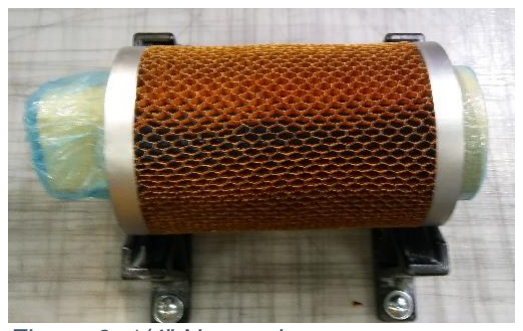
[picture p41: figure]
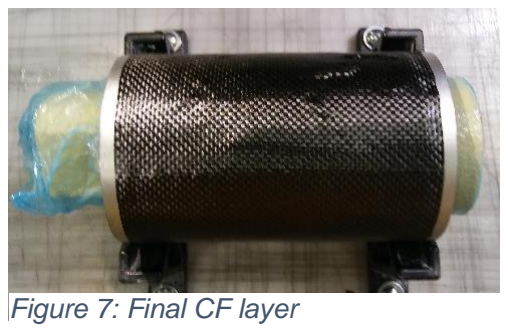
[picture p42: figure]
Figure 7: Final CF layer
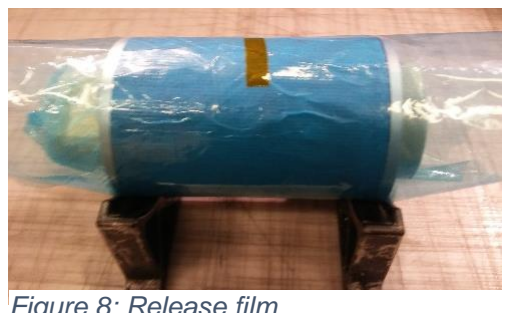
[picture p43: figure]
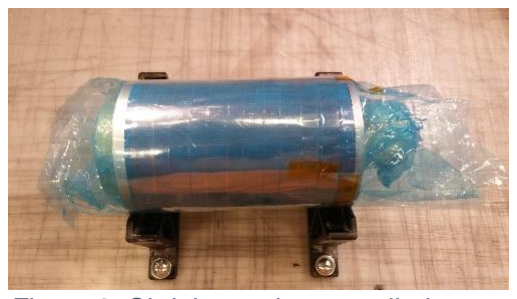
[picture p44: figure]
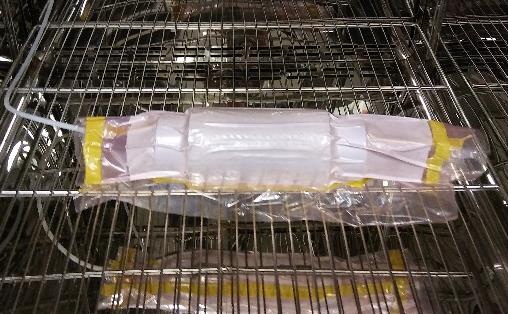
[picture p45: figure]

Figure 10: Module in vacuum bag prepared for curing

Figure 6: 1/4" Nomex layer

Figure 8: Release film

Figure 9: Shrink tape layer applied

8. Repeat steps 2 &3 carefully placing the next layer of the METLBOND adhesive.
9. Repeat step 4 using the ¼” Nomex layer.
10. Repeat steps 2 & 3.
11. Repeat steps 6 & 7.
12. Repeat steps 2 & 3 one last time.
13. Wrap a layer of release film around finished layup and secure with Kapton tape
14. Wrap shrink tape across the length of the module so that it overlaps itself (50%) on each pass. Start the wrap on the mating rings, securing it well with the kapton tape. Use a similar 2-person application process as that employed earlier. Make sure to tension the shrink tape so that it is taught, but not tight, as too much tension will put too much compression on the layup during curing. Wrap to the other mating ring and secure using kapton tape. Vacuum Bag Seal:
1. Create vacuum bag using with breather cloth and Goop tape, leaving one end open.
2. Insert tank module.
3. Seal with Goop tape, leaving a small section with the backing still attached through which the vacuum hose can be inserted when placed in the oven.

Curing Process:
1. Insert vacuum bag with secured layup into the
oven, and connect vacuum hose into open slot
in the bag. Seal with Goop tape.
2. Connect vacuum hose to vacuum pump (or other source of vacuum pressure) and open valve to create vacuum seal. Check carefully for a complete seal.
3. Turn on the oven.
4. Ramp up 50F every 20 min, until max temp of
350F is reached.
5. When 350F is achieved, hold at temperature for 2 hours.
6. When cycle is complete, turn the oven off and allow to return to ambient room temperature slowly.
7. When ambient temperature is reached, remove vacuum bag and module from the oven.

8. Remove module from vacuum bag and mandrel. It may be necessary to hammer the module off of the mandrel. Although some force may be necessary, this shall be done carefully so as to not damage the aluminum rings or cause any unnecessary stress to the module.

### Works cited:

Much credit must be given to the 2014 PSAS LV3.0 Airframe Team, as many of the materials, procedure, and initial ring design was developed through their hard work on their project. https://github.com/psas/lv3.0-airframe/blob/master/doc/mfg/LayupInstructions_2014.pdf

Ref Recommended autoclave cure cycle
https://github.com/psas/composite-propellant-tank/blob/master/Materials/Data%20Sheets%20_%20Material%20Info/Carbon%20Fiber%20Layer/3900_Prepreg.pdf (https://github.com/psas/composite-propellant-tank/blob/master/Materials/Data%20Sheets%20_%20Material%20Info/Carbon%20Fiber%20Layer/3900_Prepreg.pdf)

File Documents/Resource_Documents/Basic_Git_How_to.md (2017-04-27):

## How to Git:

Before pushing anything:

- git pull 
- git status
(make sure you are up to date)

- git add -A 
(add all local changes)
or
- git add/rm  "specific file"

- git commit -m "write your commit message here"

- git push
(push to git, duh)

- git status
(Check you're all good)

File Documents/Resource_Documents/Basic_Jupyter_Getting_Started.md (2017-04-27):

***Getting Started with Jupyter Notebooks***

**Installing Jupyter Notebook:**

1.  Download Anaconda software package which includes Python 3, Jupyter notebook, and a host of other useful analysis tools: [*https://docs.continuum.io/anaconda/install*](https://docs.continuum.io/anaconda/install)

2.  Follow these instructions if you get stuck: [*https://www.datacamp.com/community/tutorials/tutorial-jupyter-notebook\#gs.null*](https://www.datacamp.com/community/tutorials/tutorial-jupyter-notebook#gs.null)

3.  When you have it installed, you should be able to type *‘jupyter notebook*’ into command prompt, and have it open up a new window in your browser showing the directory of your active jupyter notebooks, this will likely be ‘Documents’ or another high-level user folder.

4.  Remember: when you close the browser window, that does not shut down the Jupyter kernel. To properly shut down Jupyter notebooks, go back to the command window and hit *Ctl + c* to end the session.

Jupyter notebook only has one working directory at a time, so you want to make sure that it opens up to our team’s active notebook directory, which leads me to…

**Changing/Assigning your Jupyter Notebook Directory (Windows):**

1.  If you haven’t done so already, install Gitbash and clone the PSAS/Composite Fuel Tank project directory to a desired location on your computer (make sure it is where you want it semi-permanently).

2.  Create a jupyter configuration file by entering the following into command terminal: *‘ jupyter notebook --generate-config’* This will create a configuration file in the ‘~/.jupyter’ folder on your computer. This will probably be right in your user directory.

3.  Navigate to this folder and open up the configuration file you created. You will probably want to open this with a basic text editor such as notepad.

4.  Scroll down until you find the following line:(~ line 179)

*\#c.NotebookApp.notebook\_dir = u'...current directory'*

1.  Uncomment the line by removing ‘\#’ and insert our team’s active notebook directory (~\\*composite-propellant-tank\\Analysis\\Calculations'*) where the current directory is. This will vary slightly depending upon where you put your git clone folder.

ex. My directory looks like this:

*c.NotebookApp.notebook\_dir = u'OneDrive\\CompositeTank\_Docs\\composite-propellant-tank\\Analysis\\Calculations'*

Now, save the file and restart Jupyter notebook. It should now open to this directory.

**Editing and Viewing Jupyter Notebooks:**

The browser window allows for creation and direct editing of jupyter notebooks. For basic usage- writing text and playing around with variables- this is fine; if you are interested in anything more complex, I recommend an external IED such as Pycharm, which has built-in support for Jupyter Notebooks and Git.

If you want to create a jupyter notebook for a given analysis, but are running into roadblocks, feel free to fill in an outline with needed equations and explanations. Someone with more programming experience can go in later and develop the notebook. Additionally, any additional documents (.csv data files or images) that the notebook might need should be clearly labeled and in the same folder as the notebook.

**Github Integration:**

Very Important!

Make sure you are working on the most current version of a notebook by checking for updates via gitbash.

In order for your changes or contributions to be registered, remember to push to github after every editing session.

Easiest way to do both these things:

Right click on your local \\*composite-propellant-tank* folder in windows explorer and select “Git Bash Here”. Now you are in the right directory to pull, commit, push, etc.

Jupyter Quickstart Guide: [*https://jupyter-notebook-beginner-guide.readthedocs.io/en/latest/*](https://jupyter-notebook-beginner-guide.readthedocs.io/en/latest/)

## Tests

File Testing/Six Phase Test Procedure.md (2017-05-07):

#Six Phase Test Procedure

##Phase 1:  Flat test coupons subjected to various testing procedures

* tensile test (cryo & ambient)

* thermal cycling test (looking for delamination etc after 10 cycles)

* running comparison between both procedures

* pass/fail criteria 

	* Factor of safety:  2:1

##Phase 2:  Creating physical layups/prototypes

* will all these layers actually fit together & interface without failure

* Endcap with fitting for inlet for hydrotesting (phase 3)

##Phase 3:  Hydrotest tank

* figure out the fitting which will interface with endcap and hydropump

* Determining burst pressure

* -Identifying leakage

##Phase 4:  Cryo fill cycle

* fill with liquid nitrogen, let it return to ambient temp

* repeat.  Similar testing procedure to phase 1 with coupons

##Phase 5:  Additional hydro test, after cryo-hydro testing.

* Comparison run to see how cryo filling has altered various factors, if at all

##Phase 6: Cryo fill tank with pressure release valve connected

* see how long it takes for the tank to drain (% mass loss over time)

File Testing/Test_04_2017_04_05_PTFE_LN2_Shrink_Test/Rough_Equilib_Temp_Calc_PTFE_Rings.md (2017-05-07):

## Rough Calculations for Approximating Time to Thermal Equilibrium for PTFE Test Rings in Liquid Nitrogen:

### Known Values:
c = 970 W/kgC  (*PTFE specific heat Capacity Coefficient from EngineeringToolbox.com*)

k = 0.25 W/mK  (*PTFE Thermal Conductivity Coefficient at 25C from EngineeringToolbox.com*)

m = 0.076 kg  (*Mass of Ring*)

A = 0.005m^2 (*Surface Area of Ring*)

d = 0.005 m (*Thickness of Ring*)

deltaT = 215C (*Change in Temperature, from Room to Cryo-temp*)

### Total Heat Transfered:
Q = mcdT

Q = 15849.8 Joules

### Heat Transfer Rate:
q = kA*dT /d
q = 53.75 W

### Time to Thermal Equilibrium:

T = Q/q

Time = 294.88s = **4.94 minutes**

## Conclusion:

PTFE Rings will be submerged for a minimum of **6** minutes during Liquid Nitrogen Testing, to ensure they reach maximum cryo temperature before measurement.

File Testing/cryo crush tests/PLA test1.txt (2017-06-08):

NI VI Logger                             
Created: 6/2/2017 11:09:46.396 AM Pacific Daylight Time
Number of scans: 767
Scan rate: 0.2 seconds

Row,Time,Voltage0(Voltage),Voltage1(Voltage),Voltage2(Voltage),Voltage3(Voltage)
1,11:07:02.000 AM,-0.145148,-0.150223,-1.50813,-0.519278
2,11:07:02.200 AM,-0.145148,-0.149729,-1.76244,-0.52945
3,11:07:02.400 AM,-0.144655,-0.150223,-1.50813,-0.519278
4,11:07:02.600 AM,-0.144655,-0.150223,-1.76244,-0.52945
5,11:07:02.800 AM,-0.144655,-0.150223,-1.76244,-0.519278
6,11:07:03.000 AM,-0.145148,-0.149729,-1.76244,-0.52945
7,11:07:03.200 AM,-0.145148,-0.150223,-1.50813,-0.519278
8,11:07:03.400 AM,-0.145148,-0.150223,-1.50813,-0.52945
9,11:07:03.600 AM,-0.145148,-0.150223,-1.50813,-0.539622
10,11:07:03.800 AM,-0.145148,-0.149729,-1.50813,-0.52945
11,11:07:04.000 AM,-0.145148,-0.150223,-1.25382,-0.539622
12,11:07:04.200 AM,-0.145148,-0.150223,-2.01675,-0.52945
13,11:07:04.400 AM,-0.144655,-0.150223,-1.50813,-0.52945
14,11:07:04.600 AM,-0.144655,-0.149729,-1.50813,-0.519278
15,11:07:04.800 AM,-0.144655,-0.150223,-1.50813,-0.519278
16,11:07:05.000 AM,-0.145148,-0.150223,-1.50813,-0.519278
17,11:07:05.200 AM,-0.145148,-0.149729,-1.76244,-0.52945
18,11:07:05.400 AM,-0.145148,-0.150223,-1.50813,-0.539622
19,11:07:05.600 AM,-0.145148,-0.150223,-1.50813,-0.539622
20,11:07:05.800 AM,-0.145148,-0.150223,-1.50813,-0.52945
21,11:07:06.000 AM,-0.145148,-0.150223,-1.76244,-0.519278
22,11:07:06.200 AM,-0.144655,-0.150223,-1.76244,0.0407943
23,11:07:06.400 AM,-0.144655,-0.150223,-1.25382,-0.539622
24,11:07:06.600 AM,-0.144655,-0.149729,-1.50813,-0.539622
25,11:07:06.800 AM,-0.145148,-0.149729,-1.76244,-0.539622
26,11:07:07.000 AM,-0.145148,-0.150223,-1.50813,-0.539622
27,11:07:07.200 AM,-0.145148,-0.150223,-1.50813,-0.284696
28,11:07:07.400 AM,-0.145148,-0.150223,-1.50813,-0.519278
29,11:07:07.600 AM,-0.145148,-0.150223,-1.76244,-0.52945
30,11:07:07.800 AM,-0.144655,-0.150223,-1.50813,0.0814806
31,11:07:08.000 AM,-0.144655,-0.150223,-1.50813,-0.539622
32,11:07:08.200 AM,-0.144655,-0.150223,-1.50813,-0.52945
33,11:07:08.400 AM,-0.145148,-0.150223,-1.50813,-0.519278
34,11:07:08.600 AM,-0.145148,-0.150223,-1.25382,-0.52945
35,11:07:08.800 AM,-0.145148,-0.150223,-1.50813,-0.46842
36,11:07:09.000 AM,-0.145148,-0.150223,-1.50813,-0.539622
37,11:07:09.200 AM,-0.145148,-0.150223,-1.50813,-0.0812647
38,11:07:09.400 AM,-0.145148,-0.149729,-1.50813,-0.52945
39,11:07:09.600 AM,-0.144655,-0.150223,-1.76244,-0.52945
40,11:07:09.800 AM,-0.144655,-0.150223,-1.50813,-0.52945
41,11:07:10.000 AM,-0.145148,-0.149729,-0.999515,-0.52945
42,11:07:10.200 AM,-0.145148,-0.150223,-1.50813,-0.519278
43,11:07:10.400 AM,-0.145148,-0.150223,-1.76244,-0.519278
44,11:07:10.600 AM,-0.145148,-0.150223,-1.50813,-0.519278
45,11:07:10.800 AM,-0.145148,-0.150223,-1.50813,-0.519278
46,11:07:11.000 AM,-0.145148,-0.150223,-1.50813,-0.539622
47,11:07:11.200 AM,-0.144655,-0.150223,-1.76244,-0.52945
48,11:07:11.400 AM,-0.144655,-0.150223,-1.76244,-0.539622
49,11:07:11.600 AM,-0.144655,-0.150223,-1.25382,-0.539622
50,11:07:11.800 AM,-0.145148,-0.149729,-1.50813,-0.52945
51,11:07:12.000 AM,-0.144655,-0.150223,-1.25382,-0.509107
52,11:07:12.200 AM,-0.144655,-0.150223,-1.50813,1.01663
53,11:07:12.400 AM,-0.145148,-0.150223,-1.50813,3.23404
54,11:07:12.600 AM,-0.145148,-0.150223,-1.50813,5.41075
55,11:07:12.800 AM,-0.145148,-0.150223,-1.25382,5.74642
56,11:07:13.000 AM,-0.145148,-0.150223,-1.50813,5.52264
57,11:07:13.200 AM,-0.145148,-0.150223,-1.50813,3.62119
58,11:07:13.400 AM,-0.145148,-0.150223,-1.50813,3.62056
59,11:07:13.600 AM,-0.145148,-0.150223,-1.50813,2.64408
60,11:07:13.800 AM,-0.144655,-0.150223,-1.50813,2.64408
61,11:07:14.000 AM,-0.144655,-0.150223,-1.50813,2.63391
62,11:07:14.200 AM,-0.144655,-0.150223,-1.25382,2.64408
63,11:07:14.400 AM,-0.145148,-0.150223,-1.50813,2.64408
64,11:07:14.600 AM,-0.144655,-0.150223,-1.50813,2.64408
65,11:07:14.800 AM,-0.144655,-0.150223,-1.50813,2.64408
66,11:07:15.000 AM,-0.144655,-0.150223,-1.76244,2.63391
67,11:07:15.200 AM,-0.144655,-0.149729,-2.27106,2.6034
68,11:07:15.400 AM,-0.145148,-0.150223,-1.50813,2.65425
69,11:07:15.600 AM,-0.145148,-0.150223,-1.50813,2.61357
70,11:07:15.800 AM,-0.144655,-0.149729,-1.25382,2.64408
71,11:07:16.000 AM,-0.145148,-0.150223,-1.50813,2.64408
72,11:07:16.200 AM,-0.145148,-0.149729,-1.50813,2.64408
73,11:07:16.400 AM,-0.145148,-0.150223,-1.25382,2.64408
74,11:07:16.600 AM,-0.145148,-0.150223,-1.76244,0.558909
75,11:07:16.800 AM,-0.145148,-0.150223,-1.50813,2.64408
76,11:07:17.000 AM,-0.144655,-0.150223,-1.25382,2.63391
77,11:07:17.200 AM,-0.144655,-0.150223,-1.76244,2.65425
78,11:07:17.400 AM,-0.144655,-0.150223,-1.76244,2.64408
79,11:07:17.600 AM,-0.144655,-0.150223,-1.50813,2.63391
80,11:07:17.800 AM,-0.144655,-0.150223,-1.50813,2.65425
81,11:07:18.000 AM,-0.144655,-0.150223,-1.50813,2.63391
82,11:07:18.200 AM,-0.144655,-0.150223,-1.50813,2.63391
83,11:07:18.400 AM,-0.145148,-0.150223,-1.50813,2.65425
84,11:07:18.600 AM,-0.144655,-0.149729,-1.50813,2.63391
85,11:07:18.800 AM,-0.145148,-0.150223,-1.76244,2.65425
86,11:07:19.000 AM,-0.145148,-0.150223,-1.50813,2.63391
87,11:07:19.200 AM,-0.145148,-0.150223,-1.50813,2.64408
88,11:07:19.400 AM,-0.145148,-0.150223,-1.50813,2.63391
89,11:07:19.600 AM,-0.145148,-0.150223,-1.50813,2.64408
90,11:07:19.800 AM,-0.145148,-0.150223,-1.50813,2.63391
91,11:07:20.000 AM,-0.144655,-0.149729,-1.50813,2.62374
92,11:07:20.200 AM,-0.144655,-0.150223,-1.50813,2.64408
93,11:07:20.400 AM,-0.144655,-0.150223,-1.50813,2.63391
94,11:07:20.600 AM,-0.145148,-0.150223,-1.50813,2.65425
95,11:07:20.800 AM,-0.145148,-0.150223,-1.50813,2.63391
96,11:07:21.000 AM,-0.145148,-0.149729,-1.76244,2.64408
97,11:07:21.200 AM,-0.144655,-0.150223,-1.50813,2.63391
98,11:07:21.400 AM,-0.144655,-0.150223,-1.50813,2.63391
99,11:07:21.600 AM,-0.145148,-0.150223,-1.76244,2.64408
100,11:07:21.800 AM,-0.145148,-0.150223,-1.50813,2.62374
101,11:07:22.000 AM,-0.145148,-0.150223,-1.76244,2.64408
102,11:07:22.200 AM,-0.145148,-0.150223,-1.50813,2.63391
103,11:07:22.400 AM,-0.144655,-0.150223,-2.01675,2.64408
104,11:07:22.600 AM,-0.144655,-0.150223,-1.76244,2.63391
105,11:07:22.800 AM,-0.145148,-0.150223,-1.76244,2.65425
106,11:07:23.000 AM,-0.145148,-0.150223,-1.50813,2.63391
107,11:07:23.200 AM,-0.145148,-0.150223,-1.76244,2.64408
108,11:07:23.400 AM,-0.144655,-0.150223,-1.50813,2.62374
109,11:07:23.600 AM,-0.145148,-0.150223,-2.01675,2.66443
110,11:07:23.800 AM,-0.145148,-0.150223,-1.76244,2.31859
111,11:07:24.000 AM,-0.145148,-0.150223,-1.76244,-0.519278
112,11:07:24.200 AM,-0.144655,-0.150223,-1.50813,-0.52945
113,11:07:24.400 AM,-0.144655,-0.149729,-1.25382,-0.539622
114,11:07:24.600 AM,-0.145148,-0.150223,-1.50813,-0.519278
115,11:07:24.800 AM,-0.145148,-0.149729,-1.76244,-0.52945
116,11:07:25.000 AM,-0.145148,-0.150223,-1.50813,-0.539622
117,11:07:25.200 AM,-0.144655,-0.150223,-1.50813,-0.52945
118,11:07:25.400 AM,-0.144655,-0.150223,-1.50813,-0.519278
119,11:07:25.600 AM,-0.145148,-0.150223,-1.50813,-0.539622
120,11:07:25.800 AM,-0.145148,-0.150223,-1.50813,-0.0507499
121,11:07:26.000 AM,-0.145148,-0.150223,-1.50813,-0.52945
122,11:07:26.200 AM,-0.145148,-0.150223,-1.76244,-0.52945
123,11:07:26.400 AM,-0.145148,-0.150223,-1.50813,0.0407943
124,11:07:26.600 AM,-0.145148,-0.150223,-1.50813,-0.539622
125,11:07:26.800 AM,-0.144655,-0.149729,-1.76244,-0.539622
126,11:07:27.000 AM,-0.145148,-0.150223,-1.76244,-0.539622
127,11:07:27.200 AM,-0.145148,-0.150223,-1.50813,-0.519278
128,11:07:27.400 AM,-0.144655,-0.150223,-1.50813,-0.52945
129,11:07:27.600 AM,-0.144655,-0.149729,-1.50813,-0.52945
130,11:07:27.800 AM,-0.145148,-0.149729,-1.76244,-0.539622
131,11:07:28.000 AM,-0.145148,-0.150223,-1.50813,-0.539622
132,11:07:28.200 AM,-0.144655,-0.150223,-1.76244,-0.519278
133,11:07:28.400 AM,-0.145148,-0.150223,-1.50813,-0.52945
134,11:07:28.600 AM,-0.145148,-0.150223,-1.50813,-0.539622
135,11:07:28.800 AM,-0.144655,-0.150223,-1.76244,-0.539622
136,11:07:29.000 AM,-0.144655,-0.149729,-1.76244,-0.539622
137,11:07:29.200 AM,-0.144655,-0.150223,-1.50813,-0.519278
138,11:07:29.400 AM,-0.145148,-0.150223,-1.50813,-0.52945
139,11:07:29.600 AM,-0.145148,-0.150223,-1.76244,-0.52945
140,11:07:29.800 AM,-0.144655,-0.150223,-1.50813,-0.539622
141,11:07:30.000 AM,-0.144655,-0.150223,-1.50813,-0.539622
142,11:07:30.200 AM,-0.144655,-0.150223,-1.50813,-0.539622
143,11:07:30.400 AM,-0.144655,-0.149729,-1.50813,-0.519278
144,11:07:30.600 AM,-0.145148,-0.150223,-1.50813,-0.52945
145,11:07:30.800 AM,-0.145148,-0.150223,-2.27106,-0.519278
146,11:07:31.000 AM,-0.144655,-0.150223,-1.76244,-0.539622
147,11:07:31.200 AM,-0.144655,-0.150223,-1.50813,-0.539622
148,11:07:31.400 AM,-0.144655,-0.150223,-1.50813,-0.539622
149,11:07:31.600 AM,-0.144655,-0.150223,-1.76244,-0.52945
150,11:07:31.800 AM,-0.145148,-0.150223,-1.50813,-0.52945
151,11:07:32.000 AM,-0.145148,-0.150223,-1.50813,-0.52945
152,11:07:32.200 AM,-0.145148,-0.150223,-2.01675,-0.52945
153,11:07:32.400 AM,-0.144655,-0.150223,-1.50813,-0.539622
154,11:07:32.600 AM,-0.145148,-0.150223,-1.76244,-0.539622
155,11:07:32.800 AM,-0.145148,-0.150223,-1.76244,-0.539622
156,11:07:33.000 AM,-0.144655,-0.150223,-1.76244,-0.549793
157,11:07:33.200 AM,-0.145148,-0.150223,-1.50813,-0.539622
158,11:07:33.400 AM,-0.145148,-0.150223,-1.76244,-0.52945
159,11:07:33.600 AM,-0.144655,-0.150223,-1.76244,-0.0507499
160,11:07:33.800 AM,-0.145148,-0.150223,-1.50813,-0.519278
161,11:07:34.000 AM,-0.145148,-0.150223,-1.50813,-0.519278
162,11:07:34.200 AM,-0.145148,-0.150223,-1.25382,-0.519278
163,11:07:34.400 AM,-0.145148,-0.150223,-1.50813,-0.52945
164,11:07:34.600 AM,-0.145148,-0.150223,-1.50813,-0.52945
165,11:07:34.800 AM,-0.144655,-0.150223,-1.50813,-0.52945
166,11:07:35.000 AM,-0.144655,-0.150223,-1.76244,-0.52945
167,11:07:35.200 AM,-0.144655,-0.150223,-1.50813,-0.52945
168,11:07:35.400 AM,-0.145148,-0.150223,-1.50813,-0.52945
169,11:07:35.600 AM,-0.145148,-0.150223,-1.76244,-0.519278
170,11:07:35.800 AM,-0.144655,-0.150223,-1.50813,-0.52945
171,11:07:36.000 AM,-0.145148,-0.150223,-1.50813,-0.519278
172,11:07:36.200 AM,-0.145148,-0.150223,-1.50813,-0.519278
173,11:07:36.400 AM,-0.144655,-0.150223,-1.76244,-0.519278
174,11:07:36.600 AM,-0.145148,-0.150223,-1.50813,-0.519278
175,11:07:36.800 AM,-0.144655,-0.150223,-1.76244,-0.519278
176,11:07:37.000 AM,-0.144655,-0.150223,-1.76244,-0.559965
177,11:07:37.200 AM,-0.145148,-0.150223,-1.50813,-0.549793
178,11:07:37.400 AM,-0.144655,-0.150223,-1.25382,-0.52945
179,11:07:37.600 AM,-0.145148,-0.150223,-1.50813,-0.519278
180,11:07:37.800 AM,-0.144655,-0.150223,-1.50813,-0.570136
181,11:07:38.000 AM,-0.144655,-0.150223,-1.76244,-0.539622
182,11:07:38.200 AM,-0.145148,-0.150223,-1.76244,-0.539622
183,11:07:38.400 AM,-0.145148,-0.150223,-1.50813,-0.539622
184,11:07:38.600 AM,-0.144655,-0.150223,-1.50813,-0.539622
185,11:07:38.800 AM,-0.144655,-0.150223,-1.25382,-0.539622
186,11:07:39.000 AM,-0.144655,-0.149729,-1.50813,-0.539622
187,11:07:39.200 AM,-0.145148,-0.150223,-1.76244,-0.539622
188,11:07:39.400 AM,-0.145148,-0.150223,-1.25382,-0.539622
189,11:07:39.600 AM,-0.145148,-0.150223,-1.76244,0.000107986
190,11:07:39.800 AM,-0.145148,-0.150223,-1.50813,-0.539622
191,11:07:40.000 AM,-0.144655,-0.150223,-1.50813,-0.539622
192,11:07:40.200 AM,-0.145148,-0.150223,-1.76244,-0.539622
193,11:07:40.400 AM,-0.144655,-0.150223,-1.50813,-0.539622
194,11:07:40.600 AM,-0.145148,-0.150223,-1.76244,-0.539622
195,11:07:40.800 AM,-0.144655,-0.150223,-1.50813,-0.539622
196,11:07:41.000 AM,-0.145148,-0.150223,-1.76244,-0.539622
197,11:07:41.200 AM,-0.145148,-0.150223,-1.50813,-0.52945
198,11:07:41.400 AM,-0.144655,-0.150223,-1.76244,-0.519278
199,11:07:41.600 AM,-0.144655,-0.150223,-1.50813,-0.519278
200,11:07:41.800 AM,-0.145148,-0.150223,-1.50813,-0.519278
201,11:07:42.000 AM,-0.145148,-0.150223,-1.50813,-0.519278
202,11:07:42.200 AM,-0.144655,-0.150223,-1.76244,-0.52945
203,11:07:42.400 AM,-0.145148,-0.150223,-1.76244,-0.488764
204,11:07:42.600 AM,-0.144655,-0.150223,-1.76244,-0.539622
205,11:07:42.800 AM,-0.144655,-0.150223,-1.50813,-0.539622
206,11:07:43.000 AM,-0.144655,-0.150223,-1.50813,-0.539622
207,11:07:43.200 AM,-0.144655,-0.150223,-1.76244,-0.539622
208,11:07:43.400 AM,-0.144655,-0.150223,-1.50813,-0.539622
209,11:07:43.600 AM,-0.145148,-0.150223,-1.50813,-0.539622
210,11:07:43.800 AM,-0.144655,-0.150223,-1.76244,-0.539622
211,11:07:44.000 AM,-0.144655,-0.150223,-1.76244,-0.539622
212,11:07:44.200 AM,-0.145148,-0.150223,-1.50813,-0.539622
213,11:07:44.400 AM,-0.144655,-0.150223,-1.76244,-0.539622
214,11:07:44.600 AM,-0.145148,-0.149729,-1.76244,-0.539622
215,11:07:44.800 AM,-0.144655,-0.150223,-1.76244,-0.539622
216,11:07:45.000 AM,-0.145148,-0.150223,-1.50813,-0.539622
217,11:07:45.200 AM,-0.144655,-0.150223,-1.50813,-0.549793
218,11:07:45.400 AM,-0.145148,-0.150223,-1.76244,-0.549793
219,11:07:45.600 AM,-0.144655,-0.150223,-1.76244,-0.519278
220,11:07:45.800 AM,-0.145148,-0.149729,-1.50813,-0.0609215
221,11:07:46.000 AM,-0.144655,-0.150223,-2.01675,-0.52945
222,11:07:46.200 AM,-0.145148,-0.150223,-1.25382,-0.539622
223,11:07:46.400 AM,-0.144655,-0.149729,-1.50813,-0.539622
224,11:07:46.600 AM,-0.145148,-0.149729,-1.76244,-0.539622
225,11:07:46.800 AM,-0.144655,-0.150223,-1.50813,-0.539622
226,11:07:47.000 AM,-0.145148,-0.150223,-1.50813,-0.539622
227,11:07:47.200 AM,-0.145148,-0.150223,-1.50813,-0.539622
228,11:07:47.400 AM,-0.144655,-0.150223,-1.50813,-0.539622
229,11:07:47.600 AM,-0.145148,-0.150223,-1.76244,-0.539622
230,11:07:47.800 AM,-0.144655,-0.150223,-1.50813,-0.406755
231,11:07:48.000 AM,-0.145148,-0.150223,-1.76244,0.0611375
232,11:07:48.200 AM,-0.145148,-0.150223,-1.76244,-0.539622
233,11:07:48.400 AM,-0.144655,-0.149729,-1.76244,-0.539622
234,11:07:48.600 AM,-0.145148,-0.149729,-1.76244,-0.52945
235,11:07:48.800 AM,-0.144655,-0.150223,-1.76244,-0.52945
236,11:07:49.000 AM,-0.144655,-0.150223,-1.76244,-0.52945
237,11:07:49.200 AM,-0.145148,-0.150223,-1.50813,-0.539622
238,11:07:49.400 AM,-0.145148,-0.149729,-1.76244,-0.539622
239,11:07:49.600 AM,-0.144655,-0.150223,-1.50813,-0.539622
240,11:07:49.800 AM,-0.144655,-0.150223,-1.76244,-0.539622
241,11:07:50.000 AM,-0.145148,-0.150223,-1.76244,-0.539622
242,11:07:50.200 AM,-0.144655,-0.150223,-1.76244,-0.346361
243,11:07:50.400 AM,-0.145148,-0.149729,-1.76244,-0.52945
244,11:07:50.600 AM,-0.144655,-0.150223,-1.76244,-0.52945
245,11:07:50.800 AM,-0.144655,-0.150223,-1.50813,-0.519278
246,11:07:51.000 AM,-0.144655,-0.150223,-1.50813,-0.52945
247,11:07:51.200 AM,-0.145148,-0.150223,-1.76244,-0.52945
248,11:07:51.400 AM,-0.145148,-0.150223,-1.76244,-0.519278
249,11:07:51.600 AM,-0.144655,-0.150223,-1.50813,-0.519278
250,11:07:51.800 AM,-0.145148,-0.150223,-1.76244,-0.509107
251,11:07:52.000 AM,-0.145148,-0.150223,-1.76244,-0.549793
252,11:07:52.200 AM,-0.145148,-0.150223,-1.76244,-0.52945
253,11:07:52.400 AM,-0.144655,-0.150223,-1.50813,-0.52945
254,11:07:52.600 AM,-0.145148,-0.150223,-1.76244,-0.0507499
255,11:07:52.800 AM,-0.144655,-0.150223,-1.76244,-0.519278
256,11:07:53.000 AM,-0.144655,-0.150223,-1.76244,-0.519278
257,11:07:53.200 AM,-0.145148,-0.150223,-1.76244,-0.519278
258,11:07:53.400 AM,-0.145148,-0.150223,-2.27106,-0.559965
259,11:07:53.600 AM,-0.144655,-0.150223,-1.50813,-0.712538
260,11:07:53.800 AM,-0.145148,-0.150223,-1.50813,-0.783739
261,11:07:54.000 AM,-0.145148,-0.150223,-1.76244,0.0611375
262,11:07:54.200 AM,-0.145148,-0.150223,-1.76244,-1.00751
263,11:07:54.400 AM,-0.144655,-0.150223,-1.76244,-1.00751
264,11:07:54.600 AM,-0.144655,-0.149729,-1.50813,-1.01769
265,11:07:54.800 AM,-0.145148,-0.150223,-1.50813,-1.02786
266,11:07:55.000 AM,-0.144655,-0.150223,-1.76244,-1.03803
267,11:07:55.200 AM,-0.144655,-0.150223,-1.50813,-1.05837
268,11:07:55.400 AM,-0.145148,-0.150223,-1.76244,-1.1194
269,11:07:55.600 AM,-0.145148,-0.150223,-1.50813,-0.152466
270,11:07:55.800 AM,-0.144655,-0.150223,-1.76244,-1.25163
271,11:07:56.000 AM,-0.144655,-0.150223,-2.01675,-1.333
272,11:07:56.200 AM,-0.145148,-0.150223,-1.76244,-1.43472
273,11:07:56.400 AM,-0.145148,-0.149729,-1.76244,0.000107986
274,11:07:56.600 AM,-0.145148,-0.150223,-1.50813,-1.39403
275,11:07:56.800 AM,-0.144655,-0.150223,-1.50813,-1.41438
276,11:07:57.000 AM,-0.144655,-0.150223,-1.50813,-1.40421
277,11:07:57.200 AM,-0.145148,-0.150223,-1.76244,-0.335554
278,11:07:57.400 AM,-0.145148,-0.149729,-1.50813,-1.49575
279,11:07:57.600 AM,-0.145148,-0.150223,-2.01675,-1.57712
280,11:07:57.800 AM,-0.144655,-0.149729,-2.01675,-0.0100636
281,11:07:58.000 AM,-0.144655,-0.149729,-1.76244,-0.366705
282,11:07:58.200 AM,-0.144655,-0.150223,-1.76244,-1.96364
283,11:07:58.400 AM,-0.145148,-0.150223,-2.01675,-2.00433
284,11:07:58.600 AM,-0.145148,-0.150223,-1.76244,-2.0145
285,11:07:58.800 AM,-0.145148,-0.150223,-1.76244,-2.00433
286,11:07:59.000 AM,-0.144655,-0.150223,-1.76244,-2.00433
287,11:07:59.200 AM,-0.144655,-0.150223,-2.01675,-2.06536
288,11:07:59.400 AM,-0.144655,-0.150223,-2.01675,-2.12639
289,11:07:59.600 AM,-0.144655,-0.150223,-2.01675,-2.19759
290,11:07:59.800 AM,-0.144655,-0.150223,-2.01675,-2.19759
291,11:08:00.000 AM,-0.145148,-0.149729,-2.01675,-2.30948
292,11:08:00.200 AM,-0.145148,-0.150223,-2.01675,-2.30948
293,11:08:00.400 AM,-0.144655,-0.150223,-1.76244,-2.30948
294,11:08:00.600 AM,-0.145148,-0.150223,-1.76244,-2.29931
295,11:08:00.800 AM,-0.144655,-0.150223,-1.50813,-2.30948
296,11:08:01.000 AM,-0.144655,-0.150223,-1.76244,-2.30948
297,11:08:01.200 AM,-0.144655,-0.150223,-1.76244,-2.36033
298,11:08:01.400 AM,-0.144655,-0.150223,-1.76244,-2.43154
299,11:08:01.600 AM,-0.145148,-0.150223,-1.76244,-2.47222
300,11:08:01.800 AM,-0.144655,-0.150223,-2.27106,-2.55359
301,11:08:02.000 AM,-0.145148,-0.149729,-1.76244,-2.60445
302,11:08:02.200 AM,-0.145148,-0.150223,-1.76244,-2.58411
303,11:08:02.400 AM,-0.145148,-0.149729,-2.01675,-2.59428
304,11:08:02.600 AM,-0.144655,-0.150223,-2.01675,-2.60445
305,11:08:02.800 AM,-0.144655,-0.150223,-2.27106,-2.60445
306,11:08:03.000 AM,-0.144655,-0.149729,-1.50813,-2.66548
307,11:08:03.200 AM,-0.144655,-0.150223,-1.76244,-2.75703
308,11:08:03.400 AM,-0.145148,-0.150223,-1.76244,-2.80788
309,11:08:03.600 AM,-0.144655,-0.150223,-2.01675,0.000107986
310,11:08:03.800 AM,-0.144655,-0.150223,-2.01675,-0.0100636
311,11:08:04.000 AM,-0.144655,-0.150223,-2.01675,-2.94011
312,11:08:04.200 AM,-0.144655,-0.150223,-2.01675,-2.97063
313,11:08:04.400 AM,-0.144655,-0.150223,-1.76244,-2.97063
314,11:08:04.600 AM,-0.144655,-0.150223,-2.01675,-2.97063
315,11:08:04.800 AM,-0.144655,-0.150223,-1.76244,-2.9808
316,11:08:05.000 AM,-0.144655,-0.150223,-1.76244,-2.9808
317,11:08:05.200 AM,-0.145148,-0.150223,-1.76244,-3.03166
318,11:08:05.400 AM,-0.145148,-0.150223,-2.01675,-3.10286
319,11:08:05.600 AM,-0.144655,-0.150223,-2.01675,-3.17406
320,11:08:05.800 AM,-0.145148,-0.150223,-2.01675,-0.254817
321,11:08:06.000 AM,-0.145148,-0.150223,-1.76244,-0.213495
322,11:08:06.200 AM,-0.145148,-0.150223,-2.01675,-3.28595
323,11:08:06.400 AM,-0.145148,-0.149729,-2.01675,-3.29612
324,11:08:06.600 AM,-0.145148,-0.149729,-2.01675,-3.31646
325,11:08:06.800 AM,-0.144161,-0.150223,-2.01675,-3.29612
326,11:08:07.000 AM,-0.145148,-0.150223,-2.01675,-3.27578
327,11:08:07.200 AM,-0.145148,-0.150223,-1.76244,-3.32663
328,11:08:07.400 AM,-0.145148,-0.150223,-2.01675,-3.36732
329,11:08:07.600 AM,-0.145148,-0.150223,-2.01675,0.000107986
330,11:08:07.800 AM,-0.145148,-0.150223,-2.27106,-3.43852
331,11:08:08.000 AM,-0.144655,-0.150223,-2.01675,-3.47921
332,11:08:08.200 AM,-0.145148,-0.150223,-2.01675,-3.48938
333,11:08:08.400 AM,-0.145148,-0.150223,-2.01675,-3.50972
334,11:08:08.600 AM,-0.145148,-0.150223,-2.27106,-3.55041
335,11:08:08.800 AM,-0.145148,-0.149729,-2.01675,-3.61144
336,11:08:09.000 AM,-0.145148,-0.150223,-2.27106,-3.61144
337,11:08:09.200 AM,-0.145148,-0.150223,-2.27106,-3.60127
338,11:08:09.400 AM,-0.145148,-0.150223,-2.01675,-0.0812647
339,11:08:09.600 AM,-0.145148,-0.150223,-2.01675,-3.62161
340,11:08:09.800 AM,-0.145148,-0.150223,-2.27106,-3.61144
341,11:08:10.000 AM,-0.145148,-0.150223,-2.52537,-1.44489
342,11:08:10.200 AM,-0.145148,-0.150223,-2.52537,-3.69281
343,11:08:10.400 AM,-0.145148,-0.150223,-2.52537,-3.72333
344,11:08:10.600 AM,-0.145148,-0.150223,-2.52537,-3.76401
345,11:08:10.800 AM,-0.145148,-0.150223,-2.77968,-3.78436
346,11:08:11.000 AM,-0.145148,-0.150223,-2.01675,-3.81487
347,11:08:11.200 AM,-0.145148,-0.149729,-2.01675,-0.274525
348,11:08:11.400 AM,-0.145148,-0.149729,-2.27106,-3.88607
349,11:08:11.600 AM,-0.145148,-0.150223,-2.27106,-3.8759
350,11:08:11.800 AM,-0.145148,-0.150223,-2.52537,-3.90641
351,11:08:12.000 AM,-0.145148,-0.150223,-2.77968,-3.93693
352,11:08:12.200 AM,-0.145148,-0.150223,-2.77968,-3.95727
353,11:08:12.400 AM,-0.145148,-0.150223,-2.52537,-3.95727
354,11:08:12.600 AM,-0.145148,-0.150223,-2.27106,-3.93693
355,11:08:12.800 AM,-0.145148,-0.150223,-2.77968,-3.92676
356,11:08:13.000 AM,-0.144655,-0.150223,-2.52537,-3.9471
357,11:08:13.200 AM,-0.144655,-0.149729,-2.77968,-3.95727
358,11:08:13.400 AM,-0.144655,-0.150223,-2.52537,-3.95727
359,11:08:13.600 AM,-0.145148,-0.150223,-2.77968,-3.93693
360,11:08:13.800 AM,-0.145148,-0.150223,-3.54261,-3.36732
361,11:08:14.000 AM,-0.145148,-0.150223,-3.03399,-3.98779
362,11:08:14.200 AM,-0.145148,-0.150223,-3.03399,-3.97762
363,11:08:14.400 AM,-0.145148,-0.150223,-3.03399,0.000107986
364,11:08:14.600 AM,-0.145148,-0.150223,-3.03399,-4.00813
365,11:08:14.800 AM,-0.145148,-0.150223,-3.03399,-4.00813
366,11:08:15.000 AM,-0.145148,-0.150223,-3.2883,-4.03865
367,11:08:15.200 AM,-0.145148,-0.150223,-3.2883,-4.02847
368,11:08:15.400 AM,-0.144655,-0.150223,-3.54261,-4.05899
369,11:08:15.600 AM,-0.144655,-0.150223,-3.79692,-4.05899
370,11:08:15.800 AM,-0.144655,-0.150223,-3.79692,-4.05899
371,11:08:16.000 AM,-0.145148,-0.150223,-3.79692,-4.06916
372,11:08:16.200 AM,-0.145148,-0.150223,-3.54261,-4.0895
373,11:08:16.400 AM,-0.145148,-0.150223,-4.05123,-4.07933
374,11:08:16.600 AM,-0.145148,-0.150223,-4.05123,-4.05899
375,11:08:16.800 AM,-0.145148,-0.150223,-4.05123,-4.0895
376,11:08:17.000 AM,-0.145148,-0.149729,-4.05123,-4.10985
377,11:08:17.200 AM,-0.145148,-0.149729,-4.30554,-4.09967
378,11:08:17.400 AM,-0.145148,-0.149729,-4.30554,-4.09967
379,11:08:17.600 AM,-0.145148,-0.149729,-4.30554,-4.09967
380,11:08:17.800 AM,-0.145148,-0.150223,-4.30554,-4.09967
381,11:08:18.000 AM,-0.145148,-0.149729,-4.30554,-4.10985
382,11:08:18.200 AM,-0.144655,-0.150223,-4.55985,-4.13019
383,11:08:18.400 AM,-0.144655,-0.150223,-4.55985,-4.14036
384,11:08:18.600 AM,-0.144655,-0.150223,-5.06846,-4.14036
385,11:08:18.800 AM,-0.144655,-0.150223,-5.06846,-4.18105
386,11:08:19.000 AM,-0.144655,-0.150223,-4.81415,-4.19122
387,11:08:19.200 AM,-0.144655,-0.150223,-5.32277,-4.1607
388,11:08:19.400 AM,-0.144655,-0.150223,-5.83139,-3.78436
389,11:08:19.600 AM,-0.144655,-0.150223,-5.57708,-4.20139
390,11:08:19.800 AM,-0.144655,-0.150223,-6.0857,-4.0895
391,11:08:20.000 AM,-0.145148,-0.150223,-5.83139,-0.111779
392,11:08:20.200 AM,-0.145148,-0.150223,-5.57708,-4.23191
393,11:08:20.400 AM,-0.145148,-0.150223,-5.83139,-4.22173
394,11:08:20.600 AM,-0.145148,-0.150223,-6.0857,-4.23191
395,11:08:20.800 AM,-0.145148,-0.150223,-6.0857,0.000107986
396,11:08:21.000 AM,-0.145148,-0.150223,-5.83139,-4.22173
397,11:08:21.200 AM,-0.145148,-0.150223,-5.83139,-4.24208
398,11:08:21.400 AM,-0.145148,-0.149729,-5.83139,-4.23191
399,11:08:21.600 AM,-0.145148,-0.150223,-5.83139,-4.20139
400,11:08:21.800 AM,-0.145148,-0.150223,-5.83139,-4.24208
401,11:08:22.000 AM,-0.145148,-0.150223,-5.57708,-4.24208
402,11:08:22.200 AM,-0.145148,-0.150223,-5.57708,-1.85176
403,11:08:22.400 AM,-0.144655,-0.150223,-5.83139,-4.22173
404,11:08:22.600 AM,-0.145148,-0.150223,-5.57708,-4.21156
405,11:08:22.800 AM,-0.144655,-0.150223,-5.57708,-4.23191
406,11:08:23.000 AM,-0.144655,-0.150223,-5.57708,-4.24208
407,11:08:23.200 AM,-0.144655,-0.150223,-6.0857,-4.24208
408,11:08:23.400 AM,-0.144655,-0.150223,-6.0857,-3.84539
409,11:08:23.600 AM,-0.144655,-0.150223,-5.83139,-4.21156
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

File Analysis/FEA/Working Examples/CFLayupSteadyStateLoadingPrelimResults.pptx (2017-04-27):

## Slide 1

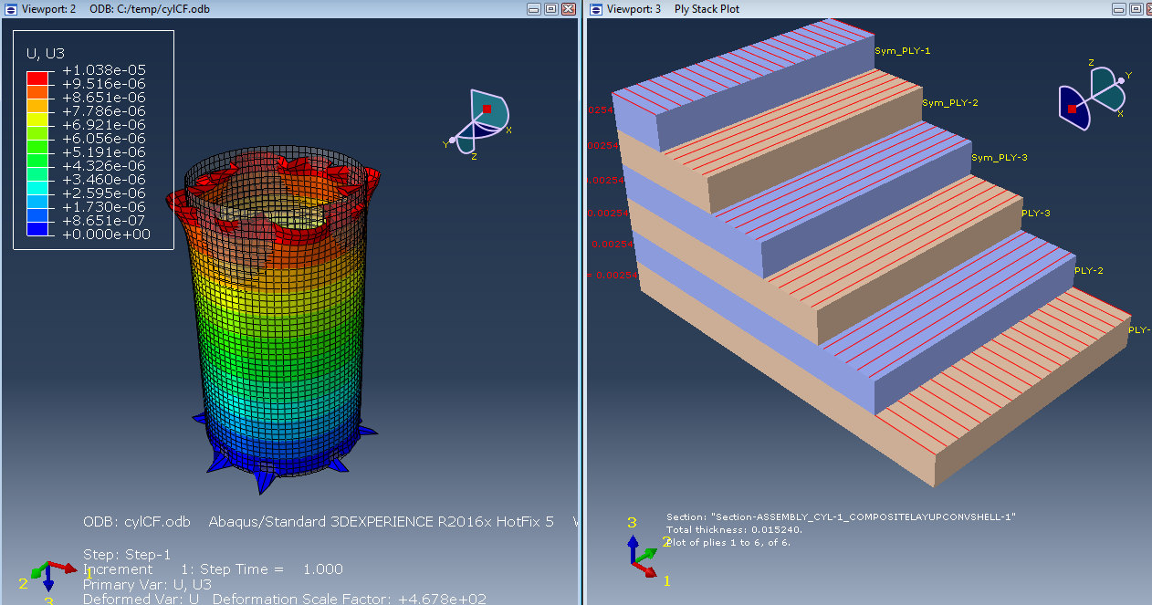
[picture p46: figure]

Z dir deformation & CF Ply orientation under 4000N top-down loading condition (prelim launch conditions) (dimensions in meters)

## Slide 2

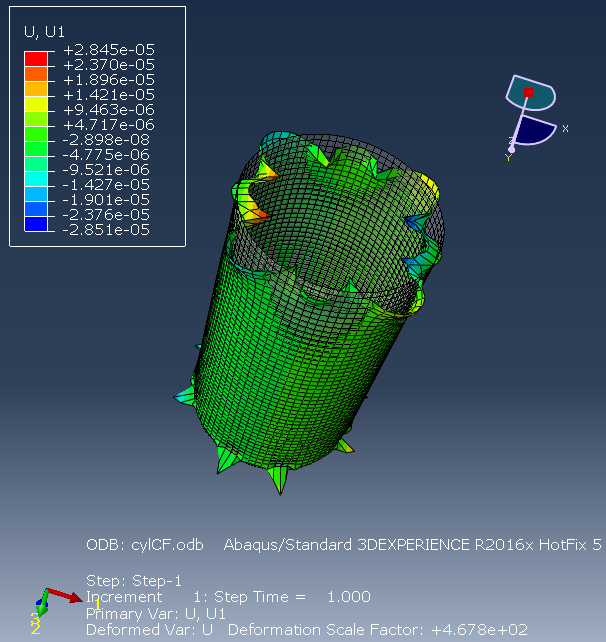
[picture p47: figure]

X dir

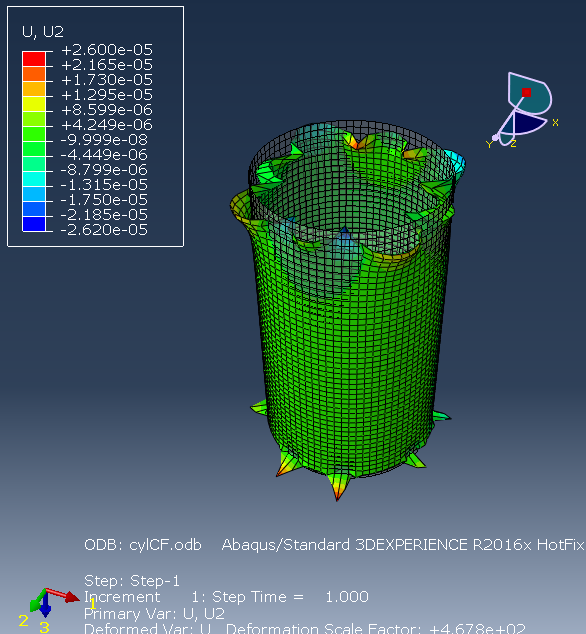
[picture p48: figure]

Y dir

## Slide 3

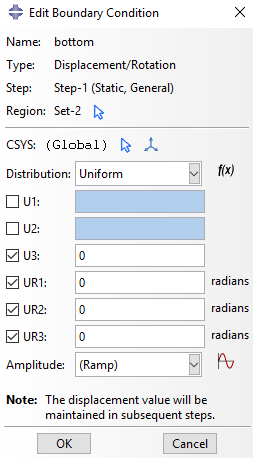
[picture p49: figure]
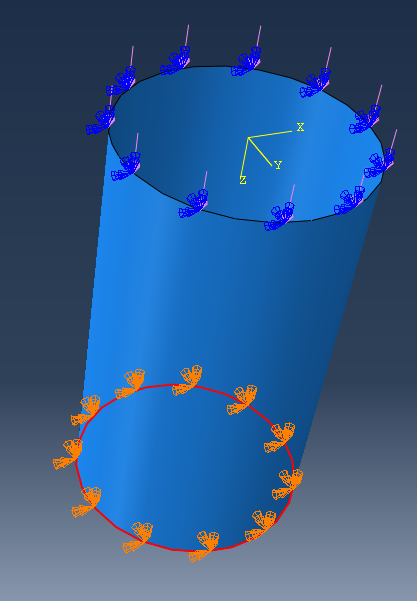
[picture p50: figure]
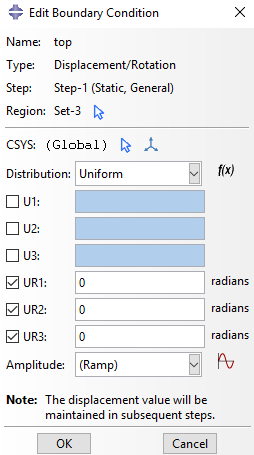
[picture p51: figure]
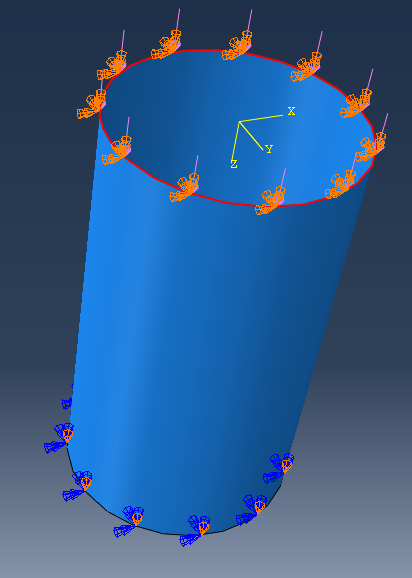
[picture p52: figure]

BC’s

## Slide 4

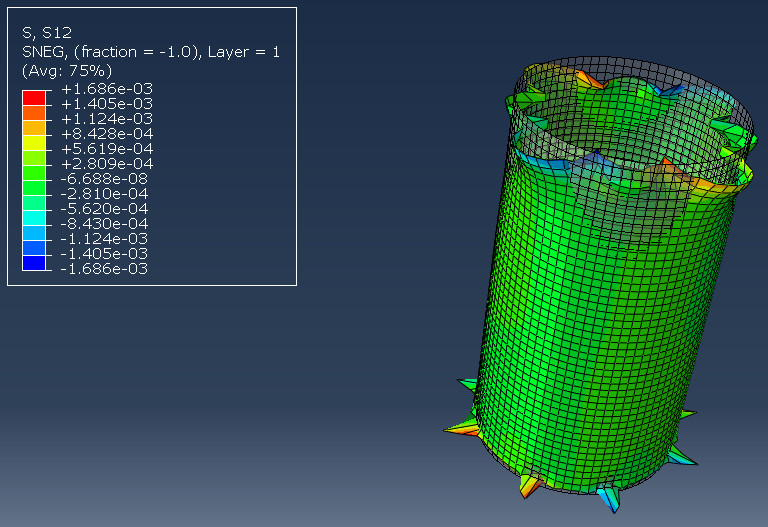
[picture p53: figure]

S12 (Shear Stress Dist)

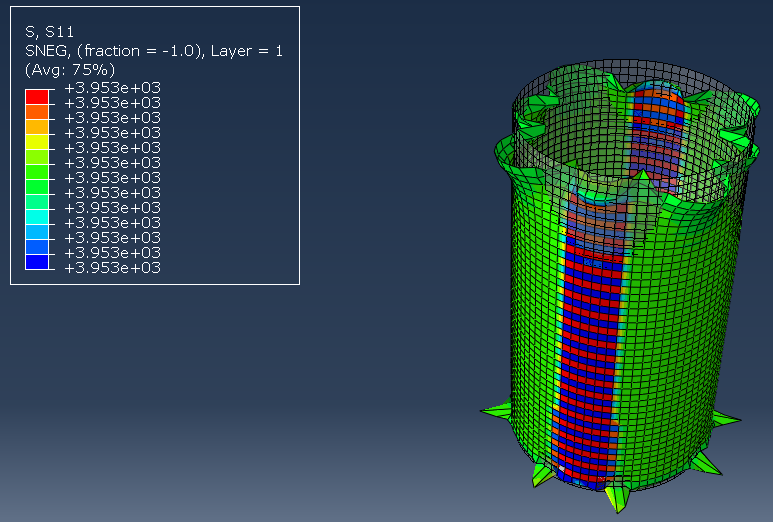
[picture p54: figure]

S11 (this looks wonky, likely due to ply stack orientation (0,90,-90)

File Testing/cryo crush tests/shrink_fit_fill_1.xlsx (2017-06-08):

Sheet: shrink_fit_fill_1
NI VI Logger
Created: 6/2/2017 11:42:53.966 AM Pacific Daylight Time
Number of scans: 515
Scan rate: 0.2 seconds
 |  |  |  | KIPS | Displ. | Kips | Displacement (inches)
Row | Time | Voltage0(Voltage) | Voltage1(Voltage) | Voltage2(Voltage) | Voltage3(Voltage) |  |  |  |  |  | 3.30524
1 | 11:40:50 | -0.145148 | -0.150223 | -1.50813 | 0.192732 | 0 | -0.04475374434 |  |  |  | 3.32558
2 | 11:40:50 | -0.145148 | -0.150223 | -1.50813 | 0.202904 | 0 | -0.04711575525 |  |  |  | 3.31541
3 | 11:40:50 | -0.145148 | -0.150717 | -1.50813 | 0.192732 | 0 | -0.04475374434 |  |  |  | 3.32558
4 | 11:40:51 | -0.145148 | -0.150223 | -1.76244 | 0.202904 | 0.25431 | -0.04711575525 |  |  |  | 3.31541
5 | 11:40:51 | -0.145148 | -0.150717 | -1.25382 | 0.132339 | -0.25431 | -0.03073005921 |  |  |  | 3.32558
6 | 11:40:51 | -0.145148 | -0.150223 | -1.25382 | 0.192732 | -0.25431 | -0.04475374434 |  |  |  | 3.31541
7 | 11:40:51 | -0.145148 | -0.150717 | -1.25382 | 0.213075 | -0.25431 | -0.04947753396 |  |  |  | 3.32558
8 | 11:40:51 | -0.145148 | -0.150223 | -1.50813 | 0.192732 | 0 | -0.04475374434 |  |  |  | 3.31541
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

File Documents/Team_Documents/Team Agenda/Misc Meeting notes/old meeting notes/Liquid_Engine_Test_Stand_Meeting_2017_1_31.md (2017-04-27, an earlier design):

Now that we have money let’s stop working on getting deals let’s just buy stuff.

Each subgroup should identify the tasks that will take the longest

**Engine**

Working on making changes for more manufacturable parts

**Github**

Create open issues and make tags so that we can see what need to be done and keep track of it getting done

We can check any repo within the PSAS org and see what things they need done and maybe do them

Make sure to close finished issues

We should check the airframe LV3.0 airframe

**They need to hydro test the tanks that they have (perhaps we can assist with that)**

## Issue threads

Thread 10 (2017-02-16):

prototype endcaps

wilsoncw6, 2017-02-16:
endcap prototypes

wilsoncw6, 2017-04-04:
currently considering a flat end cap design. Cad model has been pushed.

wilsoncw6, 2017-06-13:
We are using flat end caps with a shrink fit design.

Closed 2017-06-13.

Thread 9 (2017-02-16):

Test PTFE

wilsoncw6, 2017-02-16:
We need to test PTFE samples with our adhesive and at cryogenic temperatures.

wilsoncw6, 2017-02-28:
We did our first tests on PTFE. The metal bond works well with the etched surface. Curious to see how it will hold up at cryogenic temperatures.

wilsoncw6, 2017-04-04:
METLBOND works well with etched PTFE, still need to do cryogenic cycling.

wilsoncw6, 2017-06-13:
We found PTFE does not return to original dimensions after cycling. We are going to try cycling before turning down.

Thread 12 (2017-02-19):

Document types

7deeptide, 2017-02-19:
Suggestion: Use markdown files or something else that GitHub can natively render where possible instead of non-free `.docx` files for project documentation.

Wedon-Pete, 2017-03-02:
I can work on this as well, since I should have a documentation procedure finished up in the next couple days.  I did just add a pdf doc, and GitHub was able to render that pretty simply.  So, perhaps if we are creating documents in word, we can save them as a pdf before pushing them to Git

natronics, 2017-03-02:
The idea of git is to hold the _source_ of whatever it is you're doing. Rather than having two versions (one word doc and one pdf) of every document, it's better if you just have one version. And it's much better if that document is plain text, like markdown so it's easy to read even for people who don't have Word installed. That will also let you see what changes over time inside the file.

Wedon-Pete, 2017-03-02:
Ok, that's understandable... I'm still trying to figure this whole Git thing out.  Thanks

Wedon-Pete, 2017-03-02:
Forgive me for being a little naive with all of this (so this could be a dumb question, but I'm asking anyway), but it seems that markdown is a formatting language.  Can we just use that in notepad?

natronics, 2017-03-02:
Yes, that's right.

Anything plain text works great with git. If you add formatting like markdown, github and lots of other software will magically render it nicely. But what I mean is it should just be a text file.

Wedon-Pete, 2017-03-02:
Ok, that's what I thought.  I found several simple markdown tutorials with a quick search, so I can go through those in the next week or so and see how hard it'll be to switch things over from the word docs we've already got.

Thanks for the input.

Joedang, 2017-03-10:
There's a program called pandoc that will do this conversion for you. For example, you can give it the name of the input file and the name of the output file and it will figure out the rest.

```
$ pandoc Contacts.docx -o Contacts.md
```

As long as the content of the Word document isn't too crazy, it does what you'd expect.

Closed 2017-04-27.

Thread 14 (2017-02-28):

Pump selection for hydrotesting tank

wilsoncw6, 2017-02-28:
Research hydrotesting pumps and create a document with vendor options.
Research hydrotesting procedures. Create a draft document.

7deeptide, 2017-03-18:
@wilsoncw6 @Wedon-Pete Apart from a test procedure, is this issue still open?

Closed 2017-04-04.

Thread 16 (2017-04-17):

Stress analysis on Flat End Cap design

nab2, 2017-04-17:
Back of the envelope calculations & analysis on Flat end cap, to determine how thick it needs to be to meet FS=2, as well as any bolt sizing changes to meet FS.

RussellCBerger, 2017-04-19:
This analysis needs to be checked for errors and validity
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

wilsoncw6, 2017-06-13:
calculations are in Design\Analysis folder

Closed 2017-06-13.

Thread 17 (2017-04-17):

Heat Transfer Analysis Refinement

nab2, 2017-04-17:
Further refining heat transfer analysis to better understand overall heat xfer through tank, better represent temperatures at each interface etc..

alexkazam, 2017-04-24:
We will do the analysis with each layer experiencing the maximum change in temperature (30 C to about -190 C).

alexkazam, 2017-06-13:
See pressure vessel traditional thermal strain ipython notebook file in Analysis/Calculations folder.

Closed 2017-06-13.

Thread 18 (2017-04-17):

FEA full modeling analysis

nab2, 2017-04-17:
Begin developing full FEA model of the tank under current designs in order to locate stress concentrations due to pressure loads and thermal stresses. Will be able to use this to help determine thickness of lapping portion of ring design or any other necessary changes due to failure/stress concentrations.

nab2, 2017-06-13:
Prelim model generated, needs further refinement for any future FEA work (if applicable or deemed necessary/helpful)

Closed 2017-06-13.

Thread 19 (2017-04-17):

Gasket/Template Laser Cutting

nab2, 2017-04-17:
Arrange time with MELT to get test PTFE cut to see if lasering gaskets is feasible.  Cut gaskets, cut templates for layup procedure

andrewgreenberg, 2017-04-17:
DO NOT CUT PTFE ON THE LASER CUTTER, EVER.
Because Fluorine.

andrewgreenberg, 2017-04-17:
Huh. On the other hand, some of the interwebz disagree with me. So I guess this should be investigated. This can't be cut in the LID, for sure, but maybe with the MELT laser venting it's OK? Proceed with extreme caution, I guess.

nab2, 2017-04-17:
That was the idea.  Research done by Chris had shown that it may be ok to cut PTFE on the laser, we've been in contact with MELT already to arrange a time to do a test cut to determine if it will in fact be safe/work to our specifications.  If not we will switch to the mill or CNC.

Joedang, 2017-04-17:
> maybe with the MELT laser venting it's OK?

If they turn down the pressure on the air for the cutting head, they could get a negative gauge pressure in the machine (if it's not that way already). So, air flowing into the seams instead of out.

> we've been in contact with MELT already to arrange a time to do a test cut

Don't forget to try etching while you're at it. (Try engraving a cross-hatch pattern and a solid-fill raster, at least.)

nab2, 2017-04-17:
> Don't forget to try etching while you're at it. (Try engraving a cross-hatch pattern and a solid-fill raster, at least.)

Hm interesting point Joe.  So try to laser etch the surface for adhesion as opposed to the chemical etching we have been working with already?

Joedang, 2017-04-17:
Yeah, it wouldn't take long to try and might save a lot of time if it works.

nab2, 2017-04-17:
> Don't forget to try etching while you're at it. (Try engraving a cross-hatch pattern and a solid-fill raster, at least.)
Hm interesting point Joe. So try to laser etch the surface for adhesion as opposed to the chemical etching we have been working with already?

> Yeah, it wouldn't take long to try and might save a lot of time if it works.

@wilsoncw6

wilsoncw6, 2017-04-26:
Now that we have our PTFE sheet not just the gasket sheet I will explore this.

nab2, 2017-04-26:
> Now that we have our PTFE sheet not just the gasket sheet I will explore this.

Great thanks Chris, I think just hand cutting the sheets with a template would be ok, but would be nice to get 'exact' dimensions as this is our inner liner.  My only concern is how any of the potential etching surface will interact with the laser since we know the PTFE should be fine.  Wouldn't want any excess chemical etching stuff burning off if it is still present on that surface.

alexkazam, 2017-06-13:
Gasket design rejected.

Closed 2017-06-13.

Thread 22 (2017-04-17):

Keg Ball-Lock Connector Fittings?

nab2, 2017-04-17:
Investigate using these type of fitting instead of current selection

Joedang, 2017-04-17:
If you include things like

* what you want to solve / why this is a problem
* suggestions for how to solve the problem
* criteria for closing the issue
* links to / sketches of the thing you're talking about
* tagging/assigning people who might be able to help

it may help people jump on the issue.

nab2, 2017-04-17:
Gotcha, I'll hold off on updating more until it is a little more defined then.  This was more of a list being generated for our capstone group specifically to consolidate issues as opposed to our previous method.

Joedang, 2017-04-17:
>I'll hold off on updating more until it is a little more defined then.

I mean, having the issues made is better than not having them. I just know it's easy to forget why something was a problem, how I planned to solve it, etc.

wilsoncw6, 2017-06-13:
Did not use

Closed 2017-06-13.

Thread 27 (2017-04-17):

Composite Propellant Tank Layup Procedure

nab2, 2017-04-17:
- Need to develop clear, well-defined, easily reproducible layup procedure for manufacturing the tank. (With focus on documentation/reproducibility for future teams)
-Potential issues?  Tough layup tasks or parts to incorporate?  Securing liner, sealant, etc...
-Start documenting things early once we get all parts here and begin prototyping, much can be reiterated/recycled from LV3 airframe.
-Need a professional, clear, well-defined document before closing.

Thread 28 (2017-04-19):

Gasket/Bolt Analysis and Selection

RussellCBerger, 2017-04-19:

RussellCBerger, 2017-04-19:
Please review this for errors/validity
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

RussellCBerger, 2017-04-19:
I have the hard copies, which will be converted into a jupyter notebook file when I have time

nab2, 2017-06-13:
Closed, design rejected

Closed 2017-06-13.

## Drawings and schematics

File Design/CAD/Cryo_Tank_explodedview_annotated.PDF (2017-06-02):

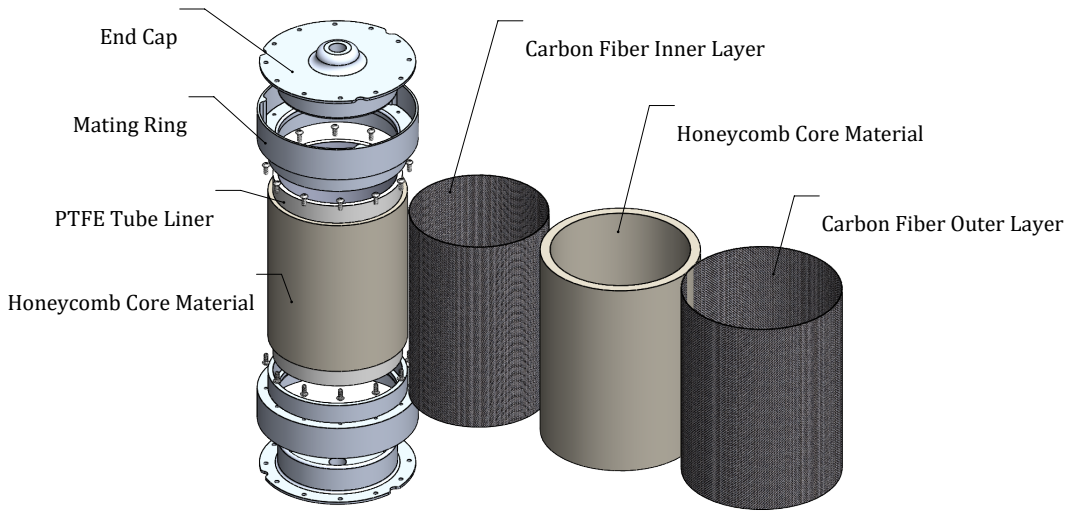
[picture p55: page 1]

End Cap
Mating Ring
PTFE Tube Liner
Honeycomb Core Material

Carbon Fiber Inner Layer
Carbon Fiber Outer Layer

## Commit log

2017-02-12 Added some stuf and things from google drive
    [BOM_draft.xlsx, Beta Accounting.xlsx, Contact Info.xlsx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]
2017-02-18 First tank ring, endcap, and liner CAD drawings
    [endcap.SLDPRT, liner.SLDPRT, mating_ring.SLDPRT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]
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2017-02-22 Basic cylinder for quote
    [6x7x.06.SLDPRT]
2017-02-23 more basic cad for quotes
    [6x7x.06.SLDDRW, 6x7x.06.SLDPRT]
2017-02-28 mating rings from lv3
    [femaleRing.SLDPRT, maleRing.SLDPRT]
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2017-03-02 Created a Budget Document
    Add real, prospective, and donated items / labor costs
    [BudgetActive.xlsx]
2017-03-07 Added 2nd version of tank CAD parts and assembly
    [Cryo Tank.SLDASM, End Cap.SLDPRT, Liner.SLDPRT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]
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2017-03-10 I've got some dimensions on these, but haven't finished doing the tolerances. I'm going to have to get a couple questions answered first, but I can try and finish up at lunch tomorrow
    [End Cap.SLDDRW, Main Ring.SLDDRW]
2017-03-19 Added male ring to CAD
    [maleRing.SLDPRT]
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2017-03-22 Removed extra requirement matrix
    [requirement_matrix.xlsx.xlsx]
2017-04-04 Made a current and archive folder for cad models and uploaded version 1.3 with a flat endcap.
    [6x7x.06.SLDDRW, 6x7x.06.SLDPRT, 90273A015_ZINC-PLATED STL FLAT HEAD PHIL MACHINE SCREW.SLDPRT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]
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2017-04-13 Updated liner thickness, added fill port fitting, changed screws
    [50785K273_MED-PRESSURE BRASS THREADED PIPE FITTING.SLDPRT, 98164A422_TYPE 316 SS BUTTON-HEAD SOCKET CAP SCREW.SLDPRT, CF Inner Layer.SLDPRT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]
2017-04-14 added new screw hole, Altered valve fitting hole size
    [50785K273_MED-PRESSURE BRASS THREADED PIPE FITTING.SLDPRT, 90273A015_ZINC-PLATED STL FLAT HEAD PHIL MACHINE SCREW.SLDPRT, 98164A422_TYPE 316 SS BUTTON-HEAD SOC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]
2017-04-16 There are now two folders one for sheet liner and one for tube liner. Also started on the drawings( not done yet).
    [50785K273_MED-PRESSURE BRASS THREADED PIPE FITTING.SLDPRT, 90273A015_ZINC-PLATED STL FLAT HEAD PHIL MACHINE SCREW.SLDPRT, 98164A422_TYPE 316 SS BUTTON-HEAD SOC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]
2017-04-17 GD&T on end cap and rings
    [End Cap.SLDDRW, Main Ring.SLDDRW]
2017-04-17 added things to the drawings
    [CF Inner Layer.SLDPRT, CF Outer Layer.SLDPRT, Cryo Tank.SLDASM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]
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2017-04-20 Added working Full model tank FEA database, edited Full modeling notes
    [FEA_Full_Tank_Model_Analysis_Workbook.xlsx]
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2017-04-21 replaced 0-80 screws with 3-48, changed tank dimensions to accomodate 1/8-inch liner thickness, increased gasket seat thickness by 1/8-inch
    [92949A325_18-8 SS BUTTON-HEAD SOCKET CAP SCREW.SLDPRT, CF Inner Layer.SLDPRT, CF Outer Layer.SLDPRT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]
2017-04-21 Created a working shrink fit model folder, with a work in progress model in it
    [50785K273_MED-PRESSURE BRASS THREADED PIPE FITTING.SLDPRT, 90273A015_ZINC-PLATED STL FLAT HEAD PHIL MACHINE SCREW.SLDPRT, 92949A325_18-8 SS BUTTON-HEAD SOCKET 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]
2017-04-21 added composite layering ex prelim work to FEA
    [FEA_Full_Tank_Model_Analysis_Workbook.xlsx]
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2017-04-24 Made a ring seal drawing for laser cutting. When cutting remember to suppress black lines)
    [Ring Seal.SLDPRT, Ring_Seal_For_laser.SLDDRW]
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2017-04-26 converted docx to md, changed dating format in meeting notes to agree with international date format
    [Copy of Availability.xlsx]
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2017-04-26 Added Steady State FEA CFLayup analysis plus some formatting edits
    [FEA_Full_Tank_Model_Analysis_Workbook.xlsx]
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2017-04-27 Added a comprehensive excel sheet with material properties
    [Materialproperties.xlsx]
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2017-04-27 finished the model for the initial shrink fit design, with interference dimensions that can be altered easily from the layout sketch in the assembly. Note: The end cap will be updated later to incorp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
    [CF Inner Layer.SLDPRT, CF Outer Layer.SLDPRT, Cryo Tank.SLDASM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]
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2017-04-27 added PTFE properties to material data excel doc'
    [Materialproperties.xlsx]
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2017-04-27 added shrink fit analysis to a second sheet on the shrink fit calc document
    [shrink_fit_calc.xlsx]
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2017-04-28 added more analysis to the shrink fit document
    [shrink_fit_calc.xlsx]
2017-04-28 Removed gasket from shrink fit design, added fillets to and cap to reduce stress concentrations
    [CF Inner Layer.SLDPRT, CF Outer Layer.SLDPRT, Cryo Tank.SLDASM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]
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2017-04-28 Changed shrink fit model end cap to have 1/4-inch FNPT hole, added keyway. Created Simplified shrink fit parts folder with simpolified end cap and ring for testing shrink fit
    [CF Inner Layer.SLDPRT, CF Outer Layer.SLDPRT, Cryo Tank.SLDASM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]
2017-04-28 Renamed parts (added part numbers to name and properties)
    [0201-B; Main Ring.SLDPRT, 0201-C; Main Ring.SLDPRT, 0202-A; Main Ring.SLDPRT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]
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2017-04-29 Somehow the screws were missing ing the sheet liner model. I put them back and moved olld screws to a folder.
    [90273A015_ZINC-PLATED STL FLAT HEAD PHIL MACHINE SCREW.SLDPRT, 92949A325_18-8 SS BUTTON-HEAD SOCKET CAP SCREW.SLDPRT, 98164A422_TYPE 316 SS BUTTON-HEAD SOCKET 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]
2017-05-03 Changed dimensions in CAD to reflect recent shrink fit analysis
    [0201-C; Main Ring.SLDPRT, 0301-C; End Cap.SLDPRT, CF Inner Layer.SLDPRT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]
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2017-05-05 Created 1/16-inch liner 'shrink fit' model, and changed 1/8'inch shrink fit model to only be compressing the liner and no aluminum
    [0201-C; Main Ring.SLDPRT, 0301-C; End Cap.SLDPRT, 50785K273_MED-PRESSURE BRASS THREADED PIPE FITTING.SLDPRT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]
2017-05-07 created STL files of Current Sheet liner endcap and mating ring
    [0202-A; Main Ring.STL, 0302-A; End Cap.SLDPRT, 0302-A; End Cap.STL]
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2017-05-19 Created flat end cap model for 1/16-inch tube liner
    [0201-B; Main Ring.SLDPRT, 0301-B; End Cap.SLDPRT, 0601-B; Ring Seal.SLDPRT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]
2017-05-31 "Lengthened rings, added three part keyways,made fill holes 7/16"
    [0201-B; Main Ring.SLDPRT, 0201-C; Main Ring.SLDPRT, 0201-C; Main Ring.STL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]
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2017-06-13 made a design folder and put cad, design ideas and analysis into it
    [0201-B; Main Ring.SLDPRT, 0201-C; Main Ring.SLDPRT, 0201-C; Main Ring.STL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]
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
